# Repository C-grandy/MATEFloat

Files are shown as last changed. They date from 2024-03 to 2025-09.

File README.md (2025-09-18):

# MATEFloat
A PCB and code for a Ranger class MATE 2024 float 
NOTE: This design should not be recreated, for reference only as it has errors 

## PCB
The PCB is based around a Atmel Atmega328p MCU interfacing with a HC-5 Bluetooth module, brushed motor driver IC, and a pressure sensor. The PCB's main purpose is to take commands over bluetooth and then dive to the bottom of a pool, find the depth, and then return to the surface and transmit the data from the pressure sensor. All electrical aspects of this system worked well, but unfortunately due to mechanical design errors the system was never tested in full capacity. 



### Power and Motor driver
The PCB features independent 3.3V and 5V linear regulators to step down a supply from two 9V batteries in parallel. The motor driver, a TI DRV8220DRLR, is powered straight from the 9V supply. The motor driver is interfaced with the MCU using two control pins, each getting proportional control via PWM. 



### Control and Communications
The system is based around a Atmel Atmega328p as it allowed for both backup software written in Arduino C++ and bare metal C for most use cases. The MCU is interfaced with a HC05 bluetooth module for communication as it was both affordable and easy to communicate to over serial UART. The float also incorporates a analog input for a pressure sensor for depth determination. A simple logic level shifter consisting of two signal MOSFETs were also included as the MCU and bluetooth module operate at different voltage levels. 



## Code
The system is programmed in AVR bare metal C, incorporating a custom made UART hardware abstraction layer (HAL) for easier to understand code. The code at its current state doesn't fully incorporate sensor readings or transmitting, but simple bluetooth communication is established. 
NOTE: The code is not at a finished state, some features work but there is limited documentation, for reference only.

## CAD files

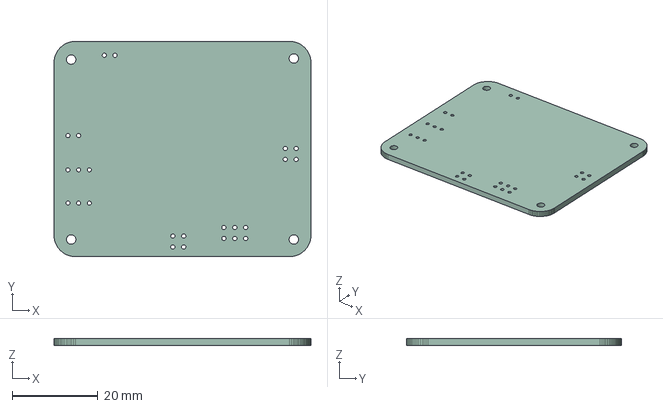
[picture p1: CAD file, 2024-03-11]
PCB/MATE ROV Float.step
60.0 x 50.2 x 1.60 mm

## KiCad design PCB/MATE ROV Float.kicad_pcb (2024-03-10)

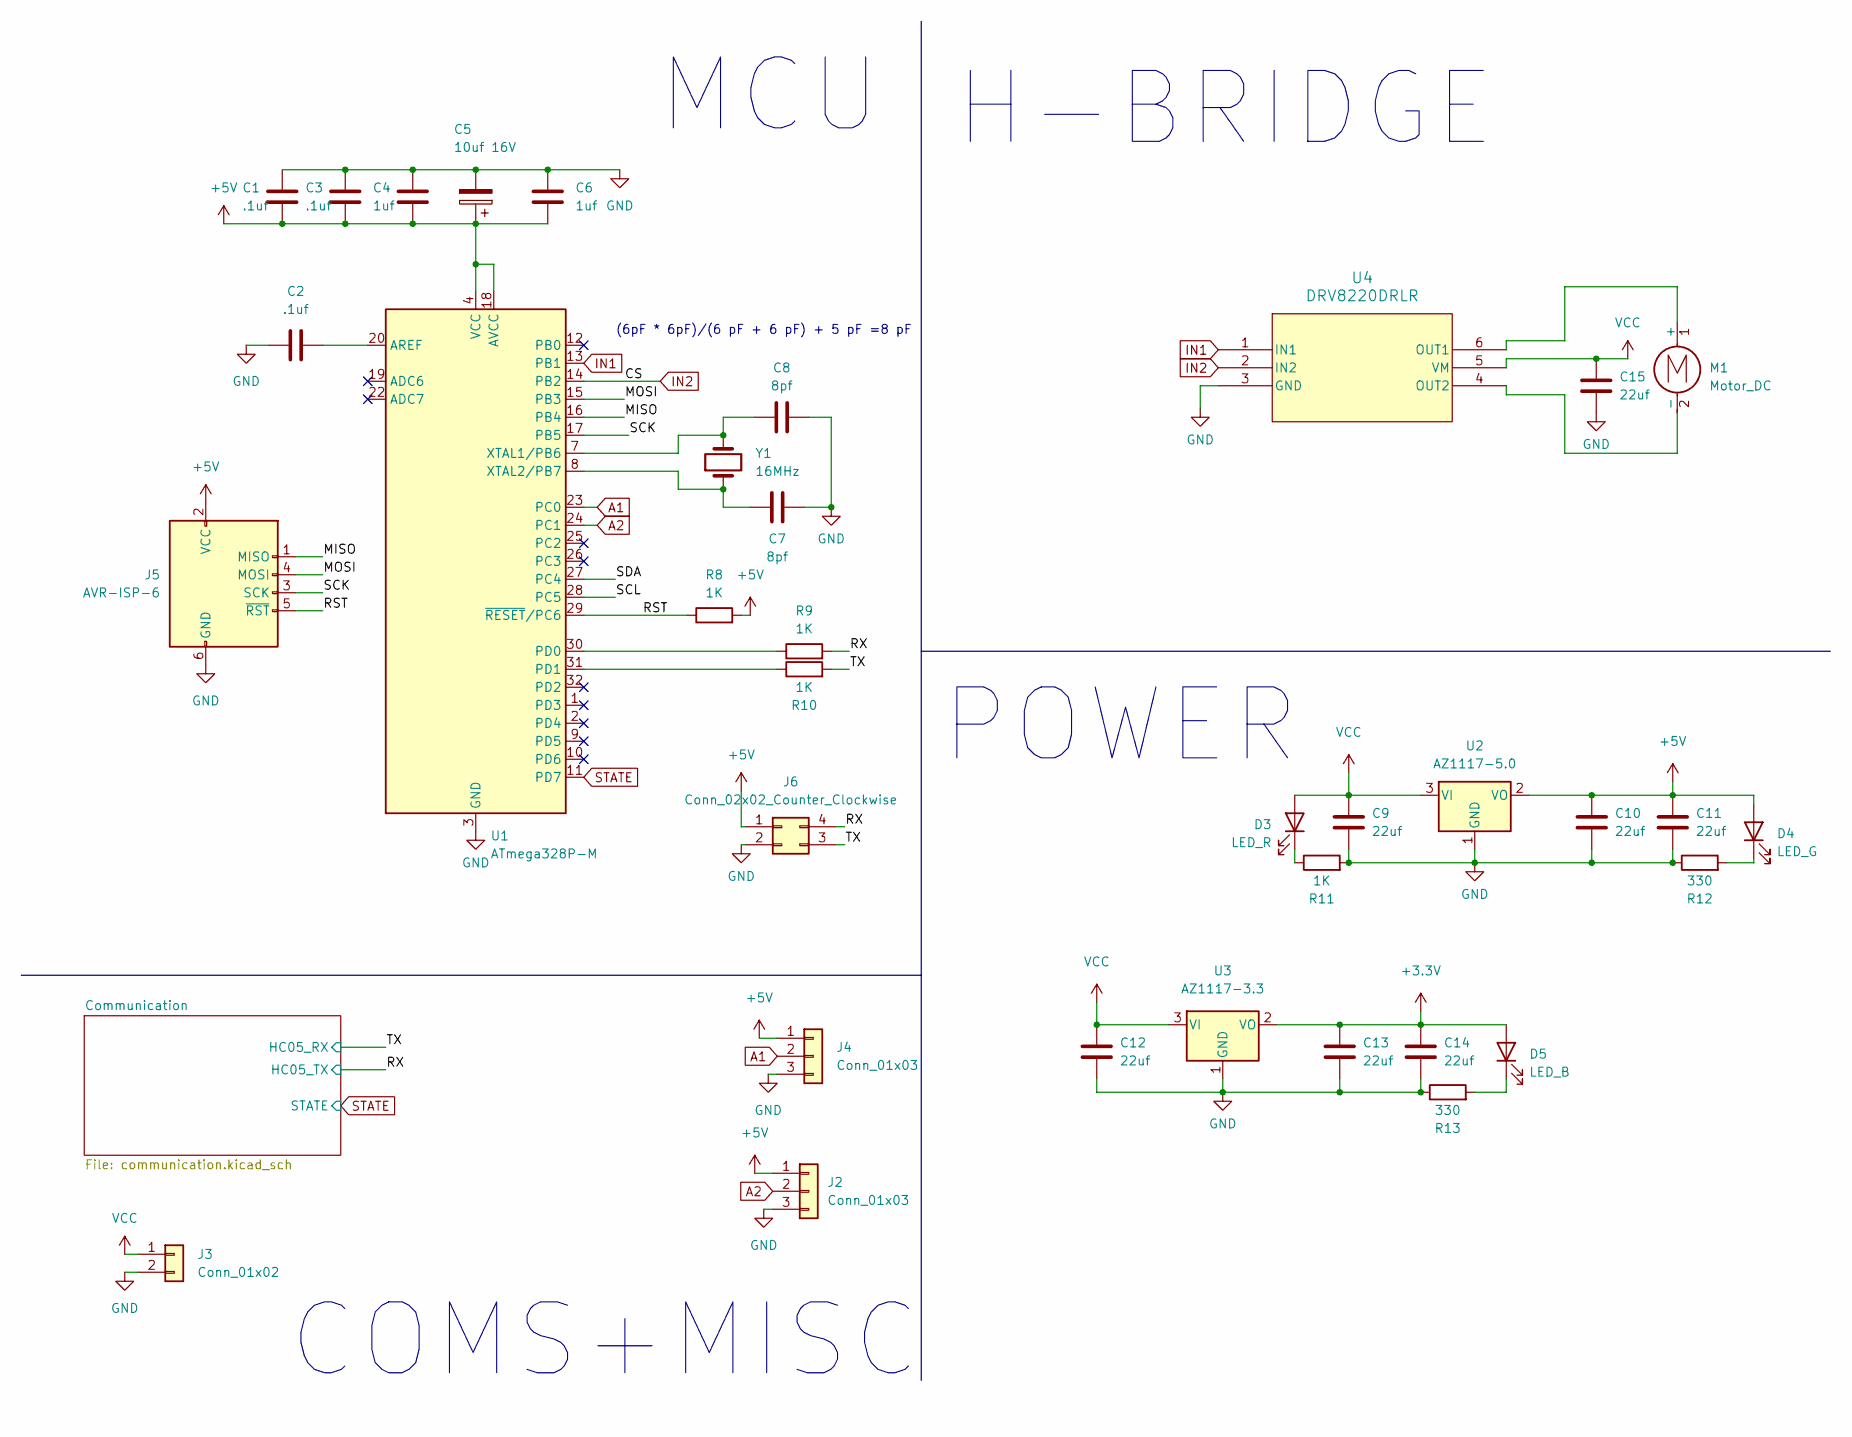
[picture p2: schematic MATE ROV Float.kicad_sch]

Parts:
C1, C2, C3: .1uf; C_0603_1608Metric_Pad1.08x0.95mm_HandSolder
C4, C6: 1uf; C_0603_1608Metric_Pad1.08x0.95mm_HandSolder
C5: 10uf 16V
C7, C8: 8pf; C_0603_1608Metric_Pad1.08x0.95mm_HandSolder
C9, C10, C11, C12, C13, C14, C15: 22uf; C_0603_1608Metric_Pad1.08x0.95mm_HandSolder
D3: LED_R; LED_0603_1608Metric_Pad1.05x0.95mm_HandSolder
D4: LED_G; LED_0603_1608Metric_Pad1.05x0.95mm_HandSolder
D5: LED_B; LED_0603_1608Metric_Pad1.05x0.95mm_HandSolder
J2, J4: Conn_01x03; JST_XH_B3B-XH-A_1x03_P2.50mm_Vertical
J3: Conn_01x02; JST_XH_B2B-XH-A_1x02_P2.50mm_Vertical
J5: AVR-ISP-6; IDC-Header_2x03_P2.54mm_Vertical
J6: Conn_02x02_Counter_Clockwise; PinHeader_2x02_P2.54mm_Vertical
M1: Motor_DC; JST_XH_B2B-XH-A_1x02_P2.50mm_Vertical
R8, R9, R10, R11: 1K; R_0603_1608Metric_Pad0.98x0.95mm_HandSolder
R12, R13: 330; R_0603_1608Metric_Pad0.98x0.95mm_HandSolder
U1: ATmega328P-M; QFN-32-1EP_5x5mm_P0.5mm_EP3.1x3.1mm
U2: AZ1117-5.0; SOT-223-3_TabPin2
U3: AZ1117-3.3; SOT-223-3_TabPin2
U4: DRV8220DRLR; SOT-563
Y1: 16MHz; Crystal_SMD_EuroQuartz_MT-4Pin_3.2x2.5mm; Part # RH100-16.000-8-2020-TR

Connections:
+3.3V: C13.1, C14.1, D5.2 (A), U3.2 (VO); also elsewhere on the board
+5V: C1.2, C3.2, C4.2, C5.1, C6.2, C10.1, C11.1, D4.2 (A), J2.1, J4.1, J5.2 (VCC), J6.1, R8.2, U1.4 (VCC), U1.6 (VCC), U1.18 (AVCC), U2.2 (VO); also elsewhere on the board
/MISO: J5.1 (MISO), U1.16 (PB4)
/MOSI: J5.4 (MOSI), U1.15 (PB3)
/RST: J5.5 (~RST), R8.1, U1.29 (~RESET/PC6)
/RX: J6.4, R9.2; also elsewhere on the board
/SCK: J5.3 (SCK), U1.17 (PB5)
/SCL: U1.28 (PC5)
/SDA: U1.27 (PC4)
/TX: J6.3, R10.2; also elsewhere on the board
A1: J4.2, U1.23 (PC0)
A2: J2.2, U1.24 (PC1)
GND: C1.1, C2.1, C3.1, C4.1, C5.2, C6.1, C7.1, C8.1, C9.2, C10.2, C11.2, C12.2, C13.2, C14.2, C15.2, J2.3, J3.2, J4.3, J5.6 (GND), J6.2, R11.2, R12.1, R13.1, U1.3 (GND), U1.5 (GND), U1.21 (GND), U1.33 (GND), U2.1 (GND), U3.1 (GND), U4.3 (GND); also elsewhere on the board
IN1: U1.13 (PB1), U4.1 (IN1)
IN2: U1.14 (PB2), U4.2 (IN2)
unnamed: D3.1 (K), R11.1
unnamed: D4.1 (K), R12.2
unnamed: D5.1 (K), R13.2
unnamed: M1.1 (+), U4.6 (OUT1)
unnamed: M1.2 (-), U4.4 (OUT2)
unnamed: C2.2, U1.20 (AREF)
unnamed: R9.1, U1.30 (PD0)
unnamed: R10.1, U1.31 (PD1)
unnamed: C8.2, U1.7 (XTAL1/PB6), Y1.2
unnamed: C7.2, U1.8 (XTAL2/PB7), Y1.1
STATE: U1.11 (PD7); also elsewhere on the board
VCC: C9.1, C12.1, C15.1, D3.2 (A), J3.1, U2.3 (VI), U3.3 (VI), U4.5 (VM)

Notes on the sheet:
POWER
COMS+MISC
MCU
(6pF * 6pF)/(6 pF + 6 pF) + 5 pF =8 pF
H-BRIDGE

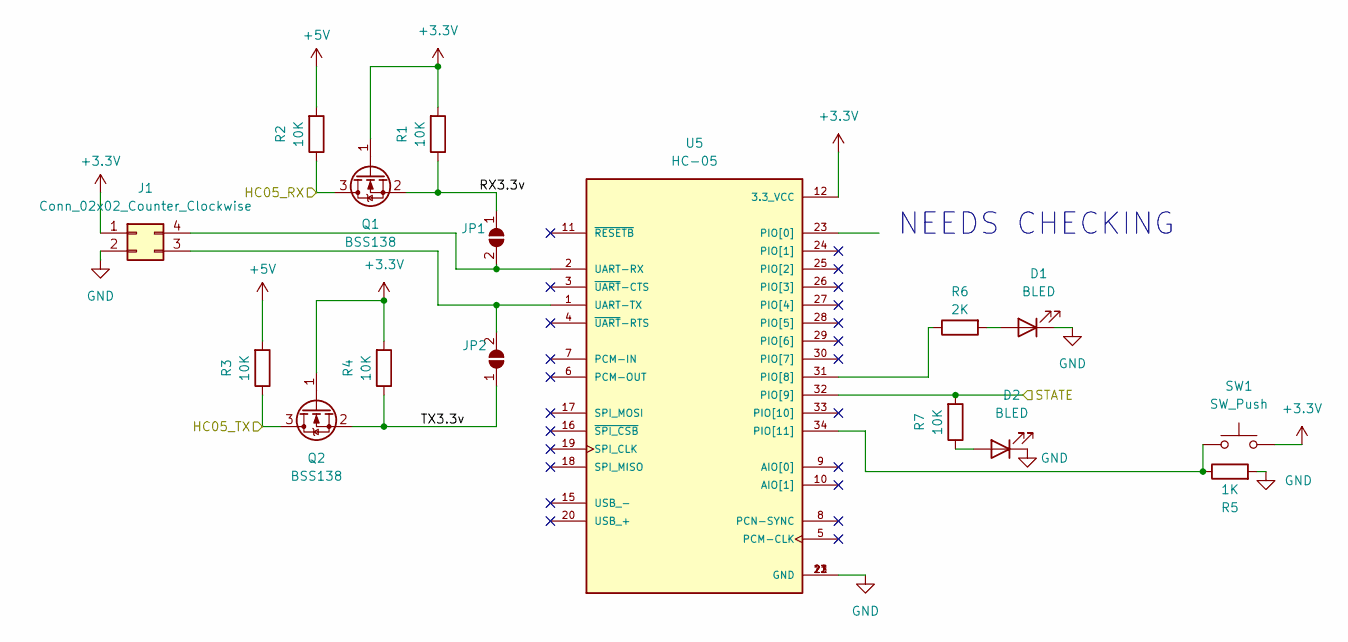
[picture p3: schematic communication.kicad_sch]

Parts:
D1, D2: BLED; LED_0603_1608Metric_Pad1.05x0.95mm_HandSolder
J1: Conn_02x02_Counter_Clockwise; PinHeader_2x02_P2.54mm_Vertical
JP1, JP2: SolderJumper_2_Open; SolderJumper-2_P1.3mm_Open_RoundedPad1.0x1.5mm
Q1, Q2: BSS138; SOT-23
R1, R2, R3, R4, R7: 10K; R_0603_1608Metric_Pad0.98x0.95mm_HandSolder
R5: 1K; R_0603_1608Metric_Pad0.98x0.95mm_HandSolder
R6: 2K; R_0603_1608Metric_Pad0.98x0.95mm_HandSolder
SW1: SW_Push; PTS526
U5: HC-05; XCVR_HC-05; PARTREV v1.0

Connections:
+3.3V: J1.1, Q1.1 (G), Q2.1 (G), R1.2, R4.2, SW1.2, U5.12 (3.3_VCC); also elsewhere on the board
+5V: R2.2, R3.2; also elsewhere on the board
/Communication /RX3.3v: JP1.1 (A), Q1.2 (S), R1.1
/Communication /TX3.3v: JP2.1 (A), Q2.2 (S), R4.1
/RX: Q2.3 (D), R3.1; also elsewhere on the board
/TX: Q1.3 (D), R2.1; also elsewhere on the board
GND: D1.1 (K), D2.1 (K), J1.2, R5.2, U5.13 (GND), U5.21 (GND), U5.22 (GND); also elsewhere on the board
unnamed: D1.2 (A), R6.2
unnamed: D2.2 (A), R7.1
unnamed: J1.3, JP2.2 (B), U5.1 (UART-TX)
unnamed: J1.4, JP1.2 (B), U5.2 (UART-RX)
unnamed: R6.1, U5.31 (PIO[8])
unnamed: R5.1, SW1.1, U5.34 (PIO[11])
STATE: R7.2, U5.32 (PIO[9]); also elsewhere on the board

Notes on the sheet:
NEEDS CHECKING

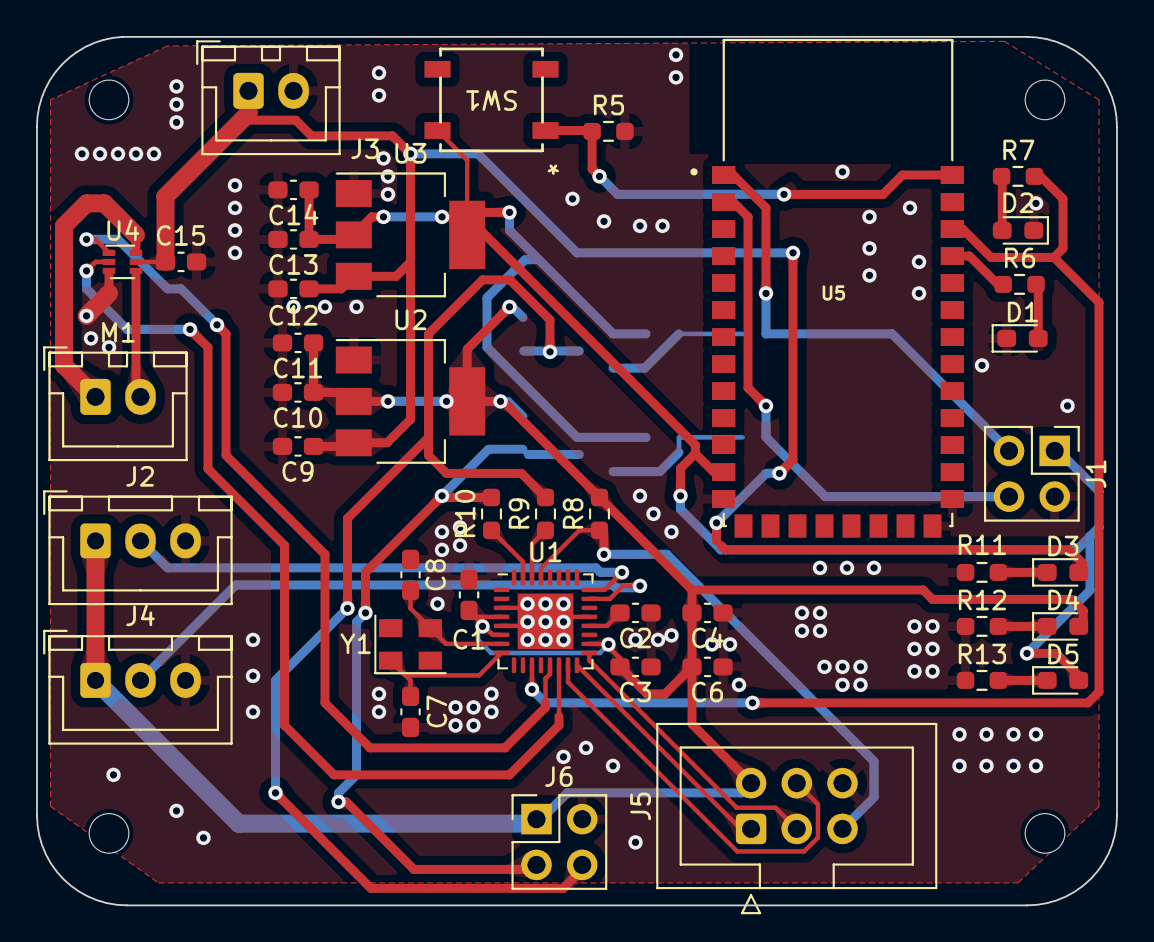
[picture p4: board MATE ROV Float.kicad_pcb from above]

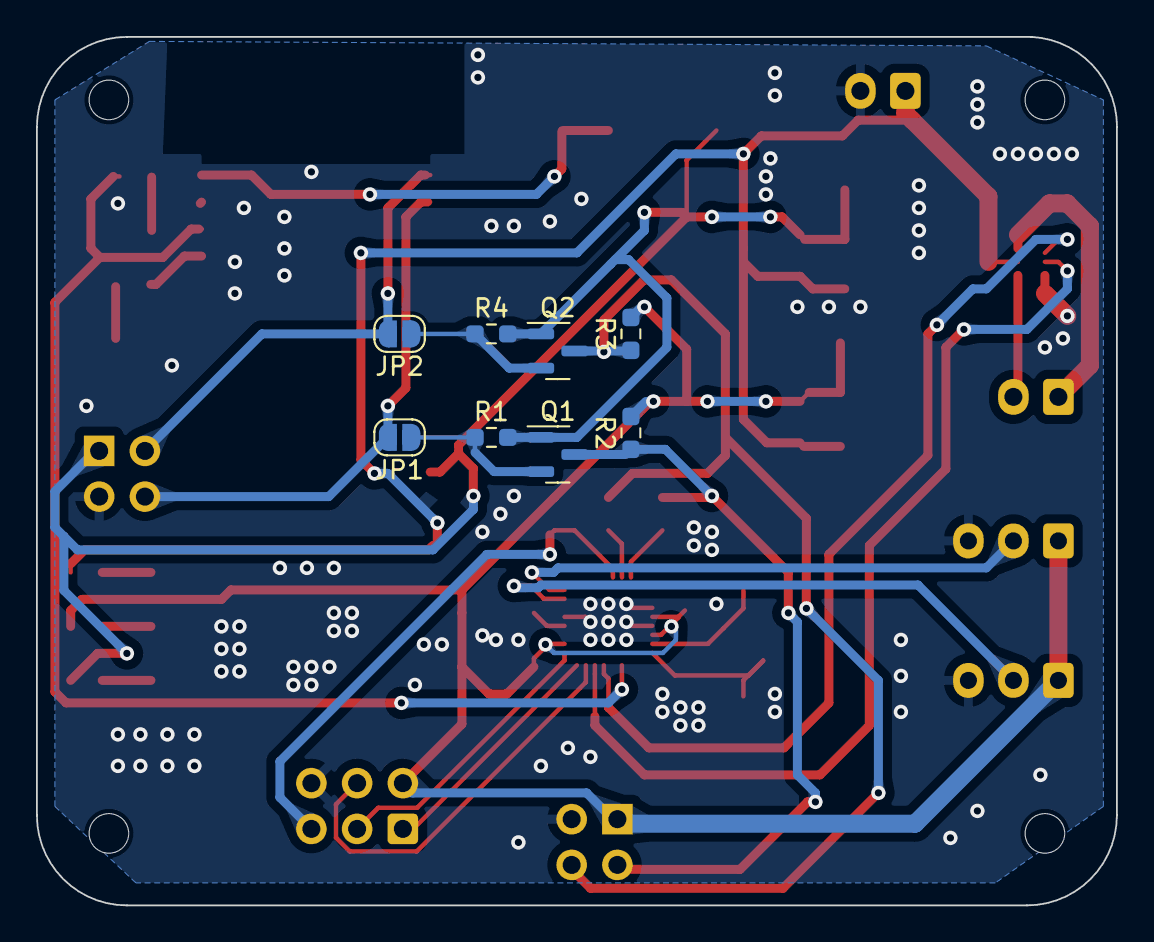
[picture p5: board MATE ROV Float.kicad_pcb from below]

Board: 2 copper layers, 60.0 x 48.2 mm, 50 parts (8 on the bottom side), 33 nets.

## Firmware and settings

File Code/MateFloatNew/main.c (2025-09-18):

/*
 * MateFloatNew.c
 *
 * Created: 4/19/2024 9:22:20 PM
 * Author : Cody G
 */ 


#include <stdint.h>
#include "config.h"
#include <avr/io.h>
#include <util/delay.h>
#include <avr/interrupt.h>
#include "uart_hal.h"
#include "ADC_DAC.h"
 uint8_t ADCVal = 0;
uint8_t rawData = 0;

int main(void)
{

	
     uint8_t start[] = "Program Start\n\r";
	uint8_t data = 0;
	uint8_t depthData[16] = {0, 0, 0, 0, 0, 0, 0, 0, 0, 0, 0, 0, 0, 0, 0, 0};
	uint8_t timeData[30] = {0};
		
	uart_init(38400,0);
	DDRB |= (1 << PB1 | 1 << PB2);
	TCCR1A |= (1 << COM1A1 | 1 << COM1B1 | 1 << WGM10);
	TCCR1B |= (1 << CS10 | 1 << WGM12);
	
	
	
	
	
	sei();
	uart_send_string(start);
	uart_send_string("Initalized");
   ADC_DAC_Setup();
   
   
   
    OCR1A = 255;
    OCR1B = 255;
	_delay_ms(1000);
	
   OCR1A = 0;
   OCR1B = 205;
   _delay_ms(35000);
   OCR1A = 205;
   OCR1B = 0;
   _delay_ms(25000);
    OCR1A = 0;
    OCR1B = 0;
   
    while (1) 
    {
		
		
		
		/*
		ADCSRA |= (1 << ADSC);
		while(!(ADCSRA & (1 << ADIF)));
		ADCSRA |= (1 << ADIF);
		*/
		//uart_send_byte(ADC_Read());
		//_delay_ms(100);
		
		//uart_send_byte(rawData);
		//_delay_ms(1000);
		
		if(uart_read_count() > 0){
			data = uart_read();
			
			//uart_send_byte(data);
			
			
			
			
			
			
			
			
				
		/* old code for on board motor driver, not working currently	
		OCR1A = 205;
			OCR1B = 0;
			_delay_ms(1000);
			OCR1A = 0;
			OCR1B = 205;
			_delay_ms(1000); */
			
			
			
			
			
			
			
			
		
		
	}
	
	
	
	
	
	switch (data) {
		
		
		case 0x31:
		uart_send_string("diving");

		OCR1A = 255;
		OCR1B = 255;
		_delay_ms(500);
		

		OCR1A = 0;
		OCR1B = 205;
	//	_delay_ms(25000);
		OCR1A = 0;
		OCR1B = 0;
		
		
		
		
		for(uint8_t i = 0; i < 30; i++){
			
			uint8_t currentPressure = (ADC_Read() - 20);
			depthData[i] = currentPressure;
			timeData[i] = ((i * 5) + 3);
			//uart_send_byte(currentPressure);
			_delay_ms(1000);
			
		}
		
		
		
		OCR1A = 0;
		OCR1B = 205;
		_delay_ms(35000);
		
		OCR1A = 0;
		OCR1B = 0;		
		data = 0;
		break;
		
		case 0x35:
		uart_send_string("Sending Data:");
		uart_send_array(depthData, 16);
		data = 0;
		break;
		
		
	}
		
	}
		
		
	}



void depthFind(){
	uint16_t rawData = 0;

	uart_send_byte(rawData);
}

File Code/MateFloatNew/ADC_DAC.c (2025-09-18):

/*
 * ADC_DAC.c
 *
 * Created: 5/8/2024 3:56:15 PM
 *  Author: Cody G
 */ 

#include "ADC_DAC.h"
 //uint16_t ADCVal = 0;

void ADC_DAC_Setup() {

ADMUX |= (1 << REFS0) |(1 << ADLAR) | (1 << MUX0);
ADCSRA |= (1 << ADEN)  | (1 << ADPS0) | (1 << ADPS1) | (1 << ADPS2);
DIDR0 |= (1 << ADC1D);

ADCSRA |= (1 << ADSC);
}







uint16_t ADC_Read(void)  {
	
	ADCSRA|=(1<<ADSC); // start conversion
	while(!(ADCSRA & (1<<ADIF))); // waiting for ADIF, conversion complete
	ADCSRA|=(1<<ADIF); // clearing of ADIF, it is done by writing 1 to it
	
	return (ADCH);
	
	
	//return ADCVal;
}
/*
ISR(ADC_vect){
	ADCVal = ADC;
	
	ADCSRA |= (1 << ADSC);
}
*/

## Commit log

2025-09-18 Update and rename Driver.kicad_sch to PCB/Driver.kicad_sch
    [Driver.kicad_sch]
2025-09-18 Update and rename MATE ROV Float.kicad_pcb to PCB/MATE ROV Float.kicad_pcb
    [MATE ROV Float.kicad_pcb]
2025-09-18 Rename MATE ROV Float.kicad_prl to PCB/MATE ROV Float.kicad_prl
2025-09-18 Rename MATE ROV Float.kicad_pro to PCB/MATE ROV Float.kicad_pro
2025-09-18 Update and rename MATE ROV Float.kicad_sch to PCB/MATE ROV Float.kicad_sch
    [MATE ROV Float.kicad_sch]
2025-09-18 Rename MATE ROV Float.step to PCB/MATE ROV Float.step
    [MATE ROV Float.step]
2025-09-18 Update and rename communication.kicad_sch to PCB/communication.kicad_sch
    [communication.kicad_sch]
2025-09-18 Update and rename fp-info-cache to PCB/fp-info-cache
2025-09-18 Rename ~MATE ROV Float.kicad_pcb.lck to PCB/~MATE ROV Float.kicad_pcb.lck
2025-09-18 Rename ~MATE ROV Float.kicad_sch.lck to PCB/~MATE ROV Float.kicad_sch.lck
